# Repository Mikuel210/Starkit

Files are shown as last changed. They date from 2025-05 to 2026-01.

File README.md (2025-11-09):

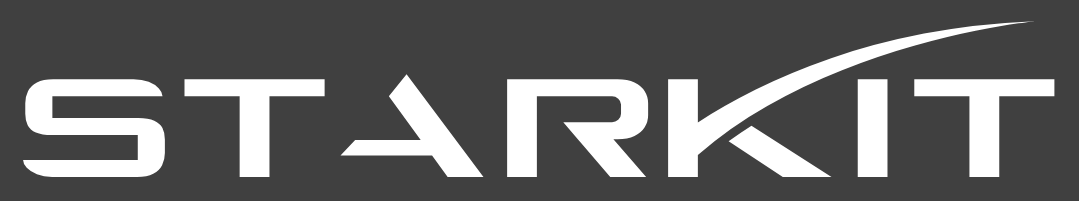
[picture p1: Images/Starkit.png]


Starkit is a thrust vector controlled electric model rocket designed for propulsive landings

<p align="center">
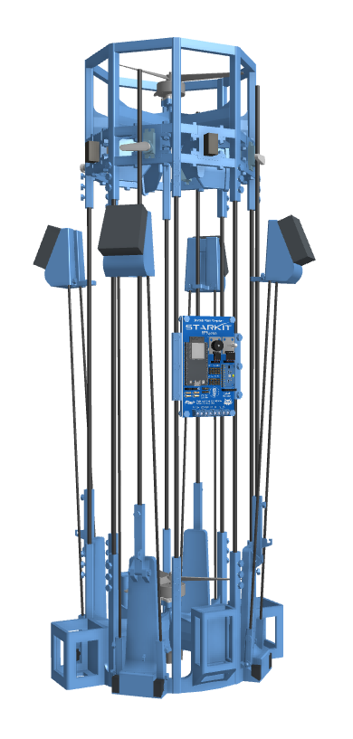
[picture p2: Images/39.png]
  
</p>

## Project description

I'm building an electric model rocket capable of taking off vertically, hovering and landing propulsively by using thrust vector control (TVC).

- **Propulsion**: I'm using two counter rotating brushless motors and 7" propellers. Each motor is powered by its own 6S LiPo battery and 60A ESC.
- **Avionics**: The main flight computer is an ESP32. I'm using an MPU9250 for orientation and a TF-Luna LiDAR for measuring altitude.
- **Control**: I'm using four TVC vanes driven by four Corona DS918MG servos.
- **Software**: I'm using PID algorithms for controlling orientation and altitude.
- **Structure**: The structure is built from 5mm carbon fiber rods. The rods are locked into 3D printed structural parts that hold mounts to attach the components as well.
- **Landing gear**: I'm using deployable landing gear, actuated by four SG90 servos. Each landing leg is made of a two part design that locks the leg in place once deployed.

## Goal of the project

**To learn and have fun by building an electric model rocket capable of lifting off, hovering and landing propulsively**

I want to build a fully reusable vehicle capable of landing propulsively through thrust vector control. If the rocket is capable of performing a 1 meter hop and hover for 30 seconds, I will consider it a success.

### Why I'm building this project

- To learn about avionics and PCB design
- To learn about software, communication and control systems
- To learn about rocket design
- To learn about CAD and project planning

## PCB

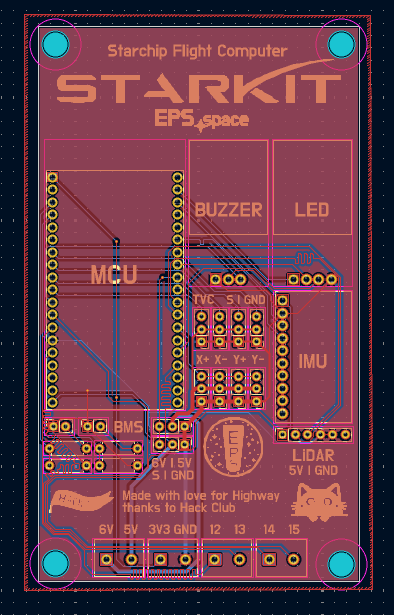
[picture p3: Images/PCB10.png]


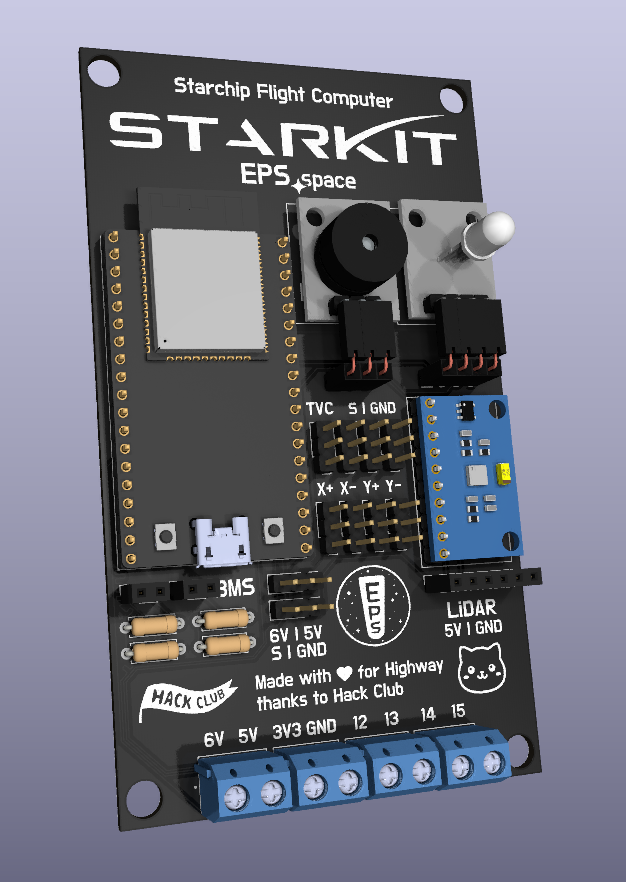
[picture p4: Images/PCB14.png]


## Wiring diagram

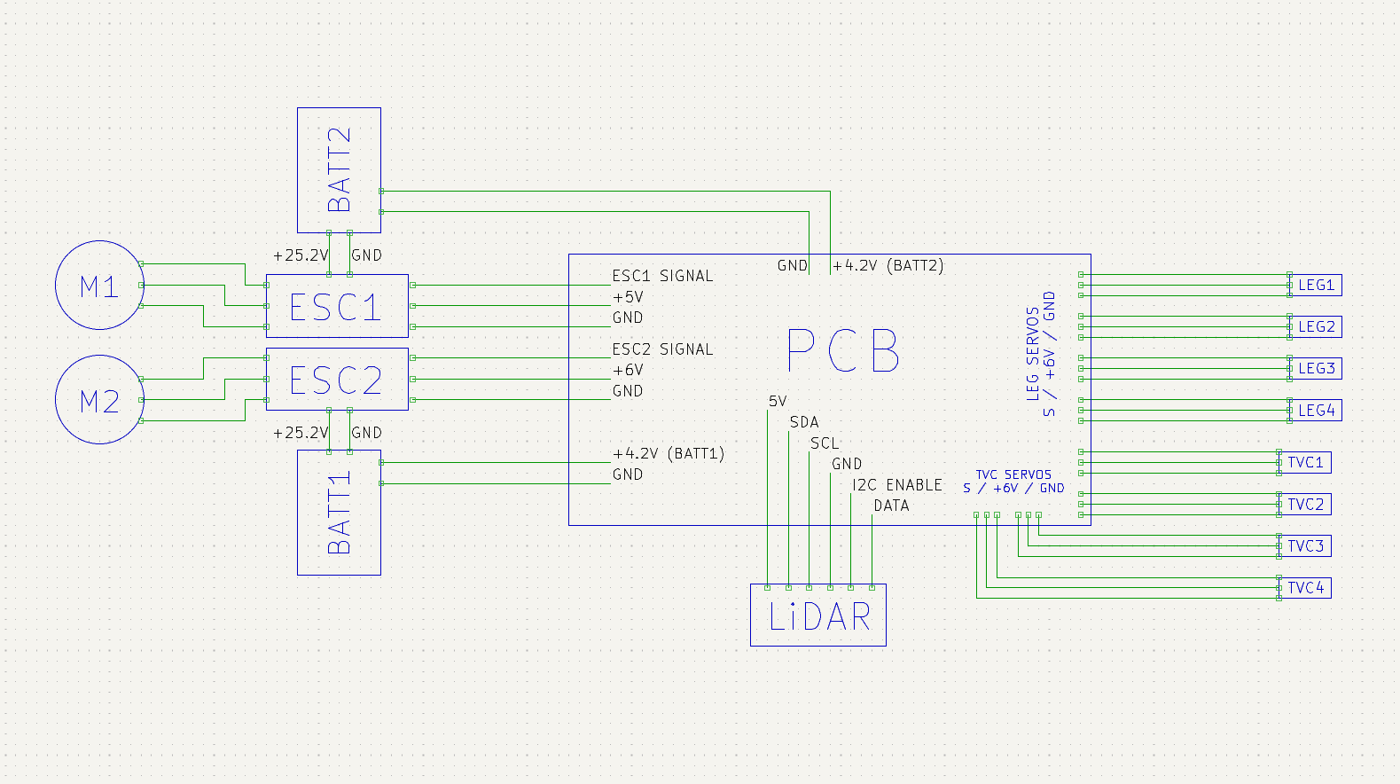
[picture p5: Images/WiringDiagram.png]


## BOM

| Item | Amount | Amount owned | Amount needed | Unit price (€) | Total price (€) | Link | Configuration |
| --- | --- | --- | --- | --- | --- | --- | --- |
| Batteries | 2 | | 2 | 21,50 € | 42,99 € | https://www.amazon.es/HRB-reemplazo-bater%C3%ADa-helic%C3%B3pteros-multicopter/dp/B08TBQKL5B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 | |
| ESCs | 2 | | 2 | 18,59 € | 37,18 € | https://es.aliexpress.com/item/1005007477046035.html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 | Flier 60A V2 |
| Motors | 2 | | 2 | 19,59 € | 39,18 € | https://es.aliexpress.com/item/1005005975992937.html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 | 1PCS KV1300 |
| Propellers | 2 | | 2 | 2,50 € | 5,00 € | https://immersion974.com/products/2-paires-dalprop-racerstar-cyclone-t7056c-7056-7x5-6x3-longue-portee-fpv-courses-helice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 | |
| Leg servos | 4 | 2 | 2 | 1,07 € | 2,13 € | https://es.aliexpress.com/item/1005006572297006.html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 | 2Pcs 180 Degree |
| TVC servos | 4 | | 4 | 9,64 € | 38,55 € | https://es.aliexpress.com/item/1005002272302617.html | With 25mm arm x4 |
| Structure rods | 20 | | 20 | 2,03 € | 40,50 € | https://es.aliexpress.com/item/1005004263451845.html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 | 5Pcs 5.0x500mm |
| Leg struts | 8 | | 8 | 0,77 € | 6,19 € | https://es.aliexpress.com/item/1005004263451845.html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 | 10Pcs 3.0x500mm |
| Leg springs | 4 | | 4 | 0,43 € | 1,73 € | https://es.aliexpress.com/item/4000250320601.html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 | 30mm 0.3 x 4 |
| PETG filament | 1 | 1 | 0 | 16,99 € | 0,00 € | https://eu.store.bambulab.com/es/products/petg-translucent?id=49192018149724 | |
| Velcro | 10 | | 10 | 0,15 € | 1,53 € | https://es.aliexpress.com/item/1005008063390791.html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 | Rectangle 16x70mm 10pcs |
| Bullet connectors | 6 | | 6 | 0,28 € | 1,66 € | https://es.aliexpress.com/item/1005006400659486.html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 | 6Pair 4.0mm |
| Cable for motor extension | 1 | | 1 | 5,59 € | 5,59 € | https://es.aliexpress.com/item/1005006566120439.html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 | 3m 12 AWG |
| Heat shrunk tubing | 1 | | 1 | 4,46 € | 4,46 € | https://es.aliexpress.com/item/1005005188307524.html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€%210%2C99€%21%21%21%21%21%40211b612817500001384372689ec846%2112000032032038883%21btf%21%21%21&afTraceInfo=1005005188307524__pc__c_ppc_item_bridge_pc_main__IQwes0f__1750000138532&gatewayAdapt=glo2esp | 580pcs in box |
| Cable for components | 1 | | 1 | 2,44 € | 2,44 € | https://es.aliexpress.com/item/1005006566120439.html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 | Black 5M 20AWG |
| Charger | 1 | | 1 | 19,67 € | 19,67 € | https://es.aliexpress.com/item/1005007326920235.html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 | |
| LiPo bag | 2 | | 2 | 5,56 € | 11,12 € | https://www.amazon.es/KUBDPQOR-bater%C3%ADa-Ign%C3%ADfuga-Explosiones-Proteger/dp/B0D6WDVMMQ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 | |
| PCB | 1 | | 1 | 0,00 € | 0,00 € | https://jlcpcb.com/es/ | |
| LiDAR | 1 | | 1 | 16,93 € | 16,93 € | https://es.aliexpress.com/item/1005007773724655.html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,scm-url:1007.40196.439370.0,pvid:257a845b-bd4b-41b9-8eb4-32116a834614,tpp_buckets:668%232846%238112%231997&pdp_ext_f=%7B%22order%22%3A%22236%22%2C%22eval%22%3A%221%22%2C%22sceneId%22%3A%2230050%22%7D&pdp_npi=4%40dis%21EUR%2157.01%2116.91%21%21%21460.14%21136.51%21%40211b680e17505431540684235eaa38%2112000042158078686%21rec%21ES%21%21ABX&utparam-url=scene%3ApcDetailTopMoreOtherSeller%7Cquery_from%3A#nav-specification | |
| IMU | 1 | | 1 | 12,29 € | 12,29 € | https://www.amazon.es/MPU%E2%80%919250-giroscopio-magn%C3%A9tico-aceleraci%C3%B3n-medici%C3%B3n/dp/B0BJ31W6KR | |
| ESP32 | 1 | | 1 | 4,99 € | 4,99 € | https://es.aliexpress.com/item/1005008256121637.html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 | 32D-Type-C-1PCS |
| Buzzer | 1 | 1 | 0 | 0,75 € | 0,00 € | https://es.aliexpress.com/item/1005007592230799.html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 | |
| LED | 1 | 1 | 0 | 0,70 € | 0,00 € | https://es.aliexpress.com/item/1005006942561228.html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 | |
| Resistors | 4 | 4 | 0 | 0,19 € | 0,00 € | https://es.aliexpress.com/item/1005007345052730.html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 | |
| Headers | 1 | | 1 | 2,02 € | 2,02 € | https://es.aliexpress.com/item/4000873858801.html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 | |
| Angled headers | 1 | | 1 | 1,24 € | 1,24 € | https://es.aliexpress.com/item/1005008210852764.html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,scm-url:1007.40196.439370.0,pvid:2362691a-9cfa-40b6-b383-5963bc6e059a,tpp_buckets:668%232846%238110%231995&pdp_ext_f=%7B%22order%22%3A%22162%22%2C%22eval%22%3A%221%22%2C%22sceneId%22%3A%2230050%22%7D&pdp_npi=4%40dis%21EUR%211.24%210.99%21%21%211.39%211.11%21%4021038df617505419994764643e6b41%2112000044248658299%21rec%21ES%21%21ABX&utparam-url=scene%3ApcDetailTopMoreOtherSeller%7Cquery_from%3A | 5Pin 5PCS |
| Screw terminals | 4 | | 4 | 0,37 € | 1,48 € | https://es.aliexpress.com/item/1005003556955422.html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 | 2Pin 5Pcs |
| Magnetic balancer | 1 | | 1 | 10,52 € | 10,52 € | https://www.amazon.es/Hobbypower-Multirotor-Propeller-Magn%C3%A9tico-Quadcopter/dp/B00GSKSFM6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 | |
| TOTAL | | | | | 309,39 € ($359.67) | | |

***

Made with ❤️ for Highway thanks to Hack Club

A badge of a Cerberus and a raccoon laughing together, with the text "HIGHWAY" and "HACK CLUB" beside them.

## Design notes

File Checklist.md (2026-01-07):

- [x] Choose a propulsion system
- [x] Choose a TVC method
- [x] Choose a structure and landing legs
- [x] CAD and simulate a 7" build
- [x] Choose avionics components
- [x] Choose servos
- [x] Choose motors, propellers and ESCs
- [x] Choose batteries and charger
- [x] Create BOM
- [x] Design PCB
- [x] Revision
- [x] Optimize PCB to use a single ESC pin and maybe use a 38 pin ESP
- [x] How am I going to cut the rods
	- Tape, hacksaw, 3D printed clamp, respirator
- [x] How am I going to build the test stand
	- Wood, bearings and 3D prints
- [x] Stuff in the diary
	- [x] Rod locking to prints
- [x] RC groups feedback
- [x] README

## After submitting

- [-] Check diameter of launch mount rails
- [x] Prototype attachments and servo mounts
	- [x] Update servo mounts to use a glued part that bolts into the thing

## After getting the grant

- [x] Buy everything except PCB
- [x] Test avionics
	- [x] Test LiDAR
	- [x] Test IMU
		- [x] Solder!
	- [x] Test TVC servos
	- [-] Make PCB circuit
- [x] Measure parts and order PCB (w/ conformal coating)
- [x] Solder PCB
	- [x] Make sure to angle the IMU headers at an angle
- [x] Prototype legs
	- [x] Change design to use bend & 500mm rods
	- [x] Update tolerances and spring thingies
	- [x] Make test pieces
	- [x] Prototype
	- [x] Change design for 500mm rods
	- [x] Reprint parts, adjusting tolerance
	- [x] Print assembly, adjust vertical tolerances
	- [x] Print deployment assembly
	- [x] Update bolt tolerance
	- [x] Make servo arm longer
	- [x] Consider foam to reduce vibrations
	- [x] Paste rods to prints tentatively
	- [x] Testing
- [x] Test PCB
- [x] Solve rod locking to prints. Test glue and bolt lock.
	- [-] Test acetone for removing resin from rods
- [x] Prototype battery, motor, rod, LiDAR, vane and ESC mounts
	- [x] Battery mount
	- [x] ESC mount
	- [x] Is the cable long enough?
	- [x] LiDAR mount
	- [x] Rod bolt attachment test
	- [x] Motor mount test
	- [x] TVC vanes (already tested for servo arm extension)
	- Conclusions
		- [x] Evaluate how much taller I can make the battery mount without interfering with the cables
		- [x] Evaluate velcro behavior
		- [x] Evaluate does the prop fit??
		- [x] I have to buy XT60 extenders because the cable isn't long enough and I don't have enough margin to move the mounts. A 3cm extension is fine (though I would check again before buying)
		- Bolt locking rods is the new standard
		- Required adjustments
			- [x] 0.5 tolerance for rods
			- [x] 5mm taller than prototype for the battery mount
			- [x] Bolt locking for all rods
			- [x] 0.5mm less width battery mount
			- [x] 1mm more width ESC mount
- [x] New CAD model
	- [x] Increased diameter
	- [x] Bolt lock is the new standard
	- [x] New airflow straighteners
	- [x] Only 1 rod segment
	- [x] Foam on the landing legs to reduce vibrations
	- [x] LiDAR under motor? 
- [-] Print another middle assembly section to test rod attachments and bolt tolerances
- [x] Decide if layout has to be changed
- [x] Test motor attachment
- [/] Printing and assembly
	- [/] Printing
		- [x] Buy filament
			- [x] Check in on Clutter grant
		- [/] Propulsion module
			- [x] Rod bolts
				- [?] Reprint them with less tolerance
			- [/] Landing legs
				- [x] Consider switching to 5mm rods
				- [-] Reprint leg tops in order to get a lower locking angle
				- [x] Reprint leg bottoms and potentially leg tips to get a stronger grip on the rods
				- [x] Redesign leg tips and bottoms for a stronger grip and straighter bolts
				- [x] Redesign leg bottom bolt
				- [x] Reprint leg parts
				- [/] Iterate on shock absorbers
				- [/] Print updated leg tip, bolts with more tolerance and cylinder with less tolerance
				- [ ] Hot glue together the perfect leg
		- [x] Guidance Assembly
			- [x] Rod bolts
			- [x] PCB bolts
		- [ ] Control assembly
			- [ ] Buy PETG
			- [ ] Rod bolts
			- [ ] Servo attachments
	- [ ] Assembly!
	- [ ] Cables
- [ ] Test motors
- [ ] Balance propellers
- [ ] Test motors w/ propellers (@ 90% thrust, they can overheat)
- [ ] Test stand assembly and PID tuning
	- [ ] Idea: Let the thing fly but tethered
- [/] Flight software
	- [x] TVC PID
	- [x] Altitude PID
	- [x] Fix TVC wiggle
	- [x] State machine
	- [x] Continuous angle (breaks at 180)
	- [x] Actuate TVC
	- [ ] Unity Simulation
		- [ ] Communication
	- [ ] Fuse altitude
	- [ ] Add BMS
		- [ ] Calibrate ADC
- [ ] Simulation
- [ ] Countdown software
- [ ] FLY IT
	- [ ] micros() will overflow after 1 hour

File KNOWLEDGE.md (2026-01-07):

**When encountering an obstacle, pause to analyze root causes instead of immediately trying random fixes.**
**Work on focused, uninterrupted sessions with no multitasking.**
**Do not cut on drying time**
**Always make test pieces before printing full parts**
**Test pieces don't always behave like full parts. Oversize holes and use another locking mechanism.**
**Don't go below the width of auto brims.**
**Do not force fits.**

Printing orientation affects the fit massively
A longer hole means more friction

- Carbon rod tolerance -> 0.5 total, use bolt
- Bolt tolerance: 0.2 -> 0.4 total

Max. spring length: >= 14cm

PLA requires ears

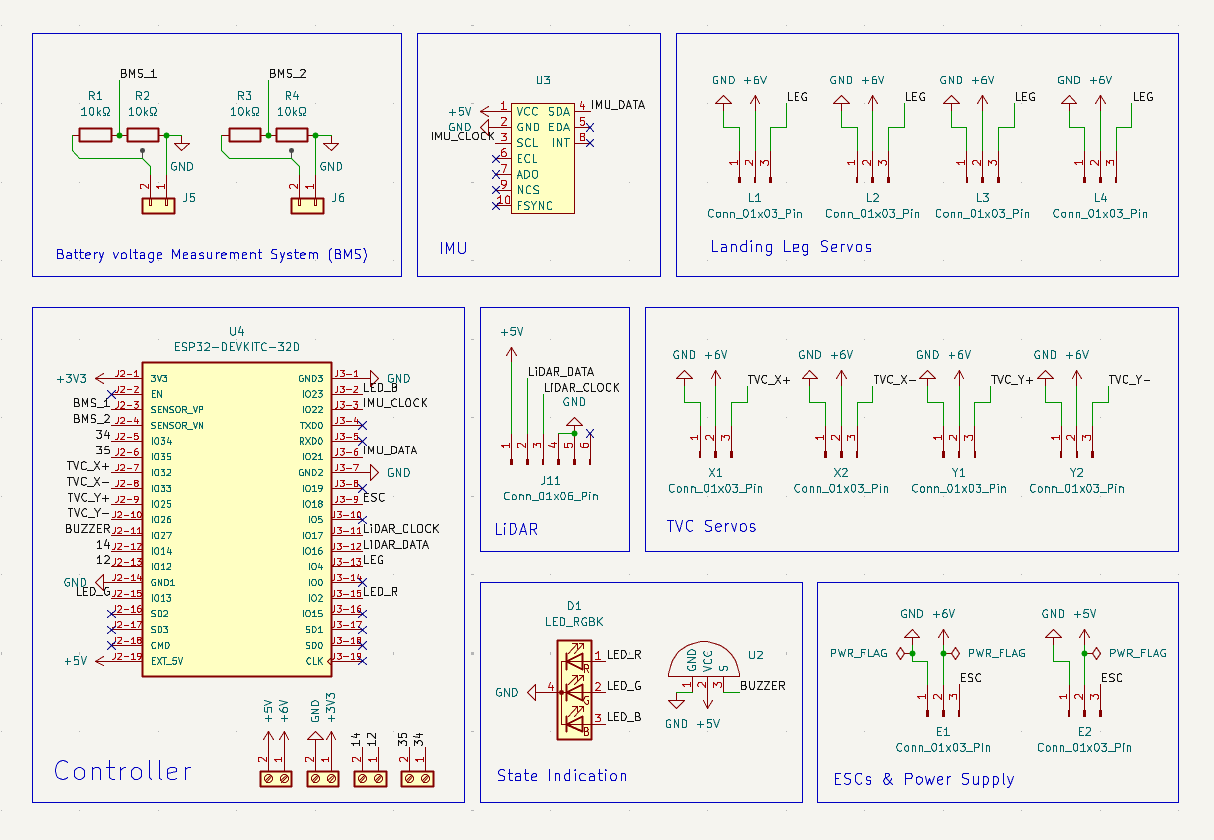
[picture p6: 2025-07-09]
Images/Schematic.png

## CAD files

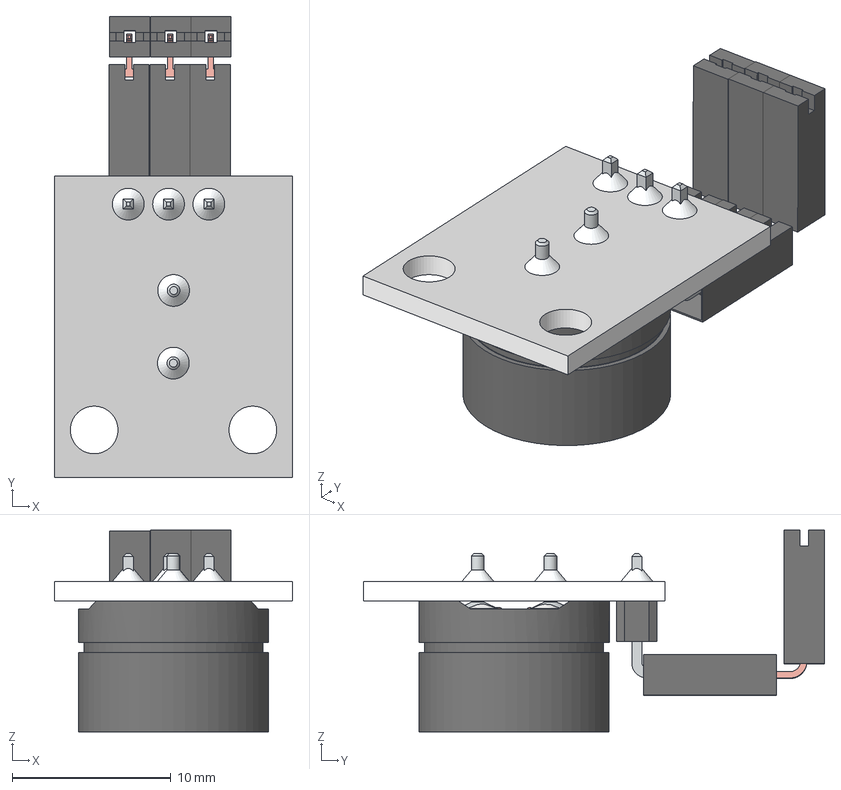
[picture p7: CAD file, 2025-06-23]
PCB/Dependencies/Buzzer.step
15.0 x 29.1 x 12.7 mm

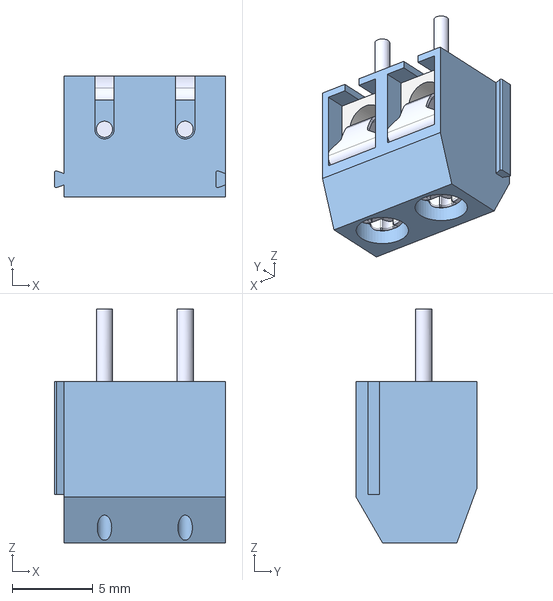
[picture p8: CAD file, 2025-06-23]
PCB/Dependencies/KF301-2P/KF301-2P.step
10.6 x 7.50 x 14.5 mm

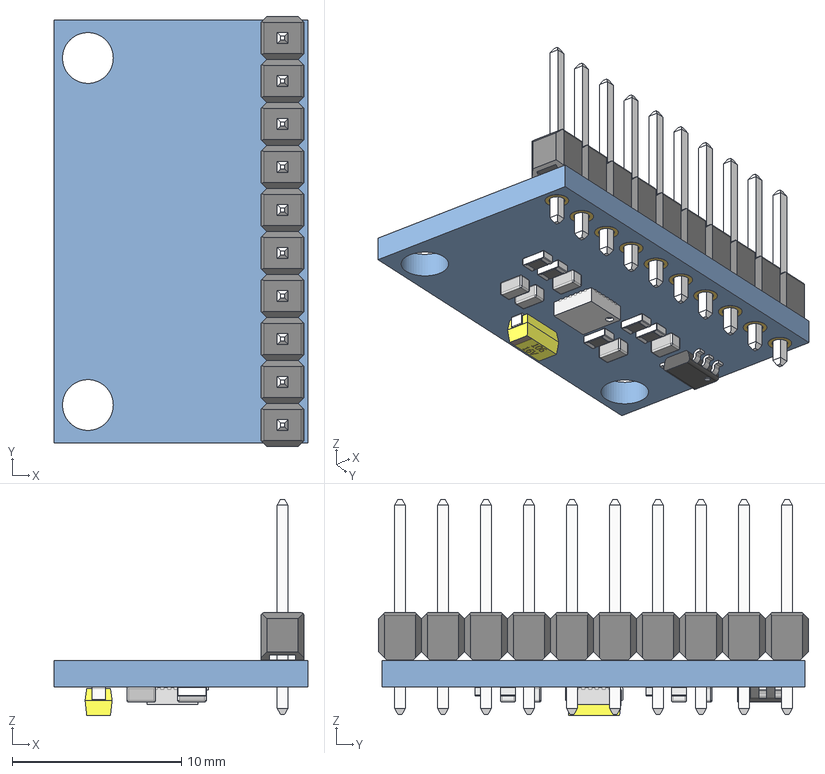
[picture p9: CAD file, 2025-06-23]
PCB/Dependencies/MPU-9250.step
15.0 x 25.4 x 12.8 mm
Pin Header 1x10 TH Pitch 2.54mm x 20
RESC-0603 x 15
CAPC-0603-T0.9-BN x 5
hole_plating x 20
tantalum 10uF
board
SOT23_5
QFN-24 3x3 0.4mm

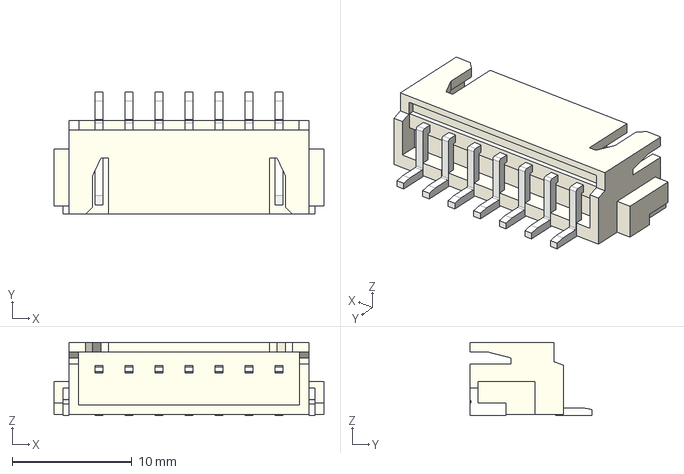
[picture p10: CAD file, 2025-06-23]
PCB/Dependencies/JST-XH7-SMD.step
22.5 x 10.2 x 6.10 mm

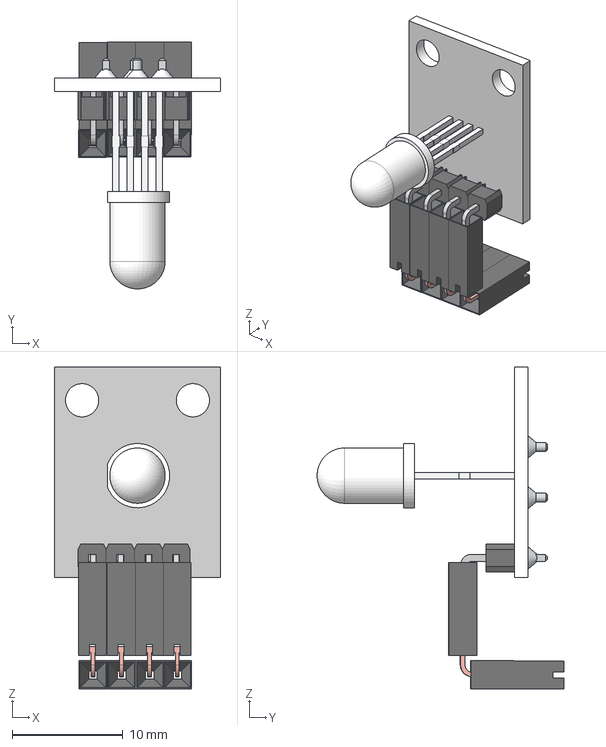
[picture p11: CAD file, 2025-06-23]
PCB/Dependencies/KY-016.step
15.0 x 22.3 x 29.1 mm

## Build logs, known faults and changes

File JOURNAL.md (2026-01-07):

---
title: "Starkit"
author: "Miguel"
description: "A thrust vector controlled electric model rocket designed for propulsive landings"
created_at: "2025-05-20"
---

## May 22: Initial ideas and goal of the project

I always like to begin engineering projects by setting a goal. For this project, my goal is the following:

**To learn and have fun by building an electric model rocket capable of lifting off, hovering and landing propulsively**

I want to build a fully reusable vehicle capable of landing propulsively through thrust vector control. If the rocket is capable of performing a 1 meter hop and hover for 30 seconds, I will consider it a success.

Based on my vision for this project, I've set some design requirements. This way, I will try to find the most efficient and cost-effective way possible of creating something that I'll be happy with:

### Design requirements

These are the absolute musts that a design should have:

- The rocket is powered by electric propulsion for cheap and safe flights and fast turnarounds
- The rocket is fully reusable and uses thrust vectoring to lift off, hover and land propulsively
- The rocket can perform a 1 meter hop and hover for 30 seconds
- The rocket is modular

  - Components are easily accessible and replaceable
  - The rocket is designed for a future launchpad integration

    _If I achieve reliable landings, I might try to build a launchpad to launch and catch the rocket from. The rocket should be modular and be designed with this in mind._

    - The rocket has got detachable or deployable landing legs and attachable catch pins
    - The pad should be able to hold the rocket until full throttle is reached

### Dream goals

These are not essential but they'd be cool to have:

- The rocket can perform a 10 meter hop
- The rocket can hover for a minute
- The rocket looks as cool as possible

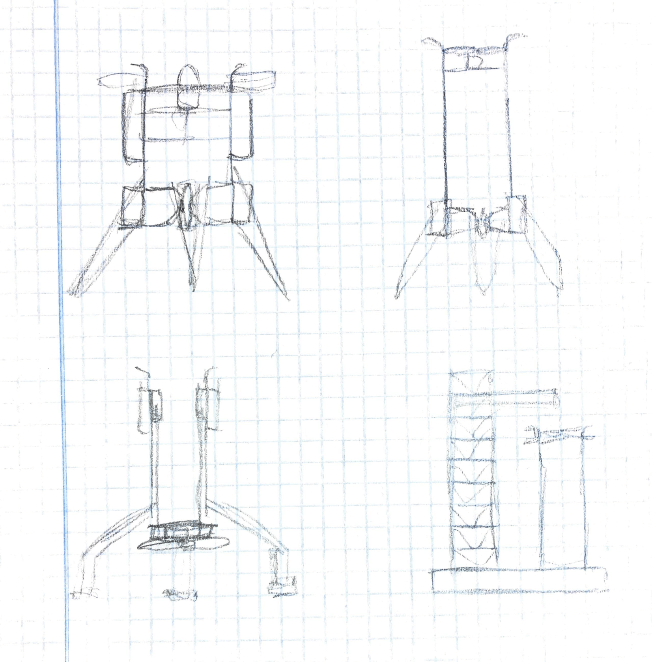
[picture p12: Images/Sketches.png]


_Initial ideas and concepts of possible designs_

**Time spent: 1h 15min**

## May 24 Log 1: Research on propulsion systems

I've decided to choose a propulsion system first and then work around that. Some options I think would fit this project are:

- Single EDF (Electric Ducted Fan)
- Single propeller
- Counter-rotating propellers
- Ducting a propeller(s) myself

The main things I've learnt today are:

- Ducting a propeller can increase efficiency and thrust.
- EDFs take advantage of this. An added benefit is that they often have stator vanes that minimize the torque produced by spinning the propeller.
- A larger propeller is usually more efficient and provides more thrust. A larger propeller could match the thrust of a smaller EDF while being less expensive, however the torque and gyroscopic effects become greater the more you scale the propeller.
- If I use a single propeller I probably wouldn't want to duct it myself as it could actually decrease the performance (EDFs are propeller and duct combinations specifically made to work together).

I've discarded ducting a propeller myself. However, I still have to make more research to figure out what the best option is. If I manage to overcome the gyroscopic effects, a single propeller would be a nice option over an EDF, as it would be less expensive. Counter-rotating propellers would also be a good option as they cancel their torque, but I still have to research if the thrust of two propellers in series is just the sum of their individual thrust.

**Time spent: 2h 30min**

## May 24 Log 2: Research on counter-rotating propellers

The reasons I would choose counter-rotating propellers over a single propeller are:

1. They cancel their torque, which means that they don't apply any rotational force to the vehicle and you don't have to worry about gyroscopic effects.
2. You have some control authority in the roll axis. If the rocket gains angular speed, you can correct it by adjusting the throttle of each individual motor. This also allows me to only use 2 servos for TVC, as you only need to correct 2 axis.

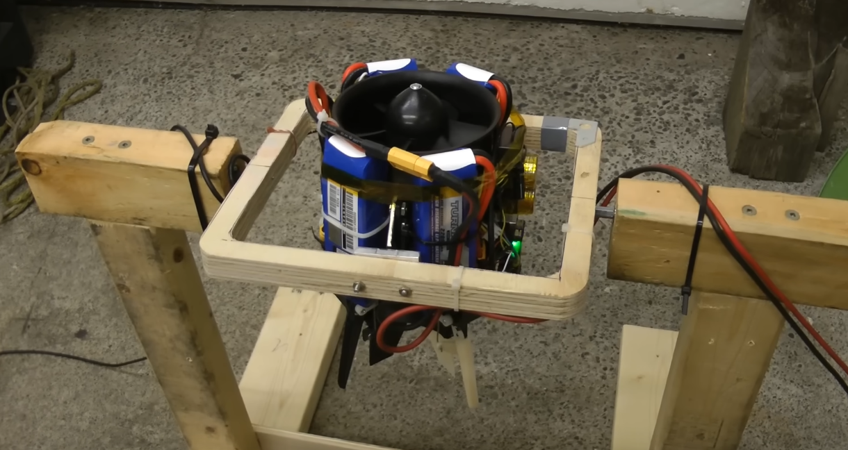
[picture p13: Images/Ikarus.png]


_The Ikarus model rocket had an issue where whenever it wanted to apply a torque through TVC, it had to apply a perpendicular torque as well due to the gyroscopic effects of a single propeller. In the Ikarus II rocket this problem was solved by using counter-rotating EDFs._

Placing the propellers one after the other would decrease thrust and efficiency. However, if I keep the propellers spaced and use airflow straighteners for feeding the second propeller cleaner air, this could be mitigated.

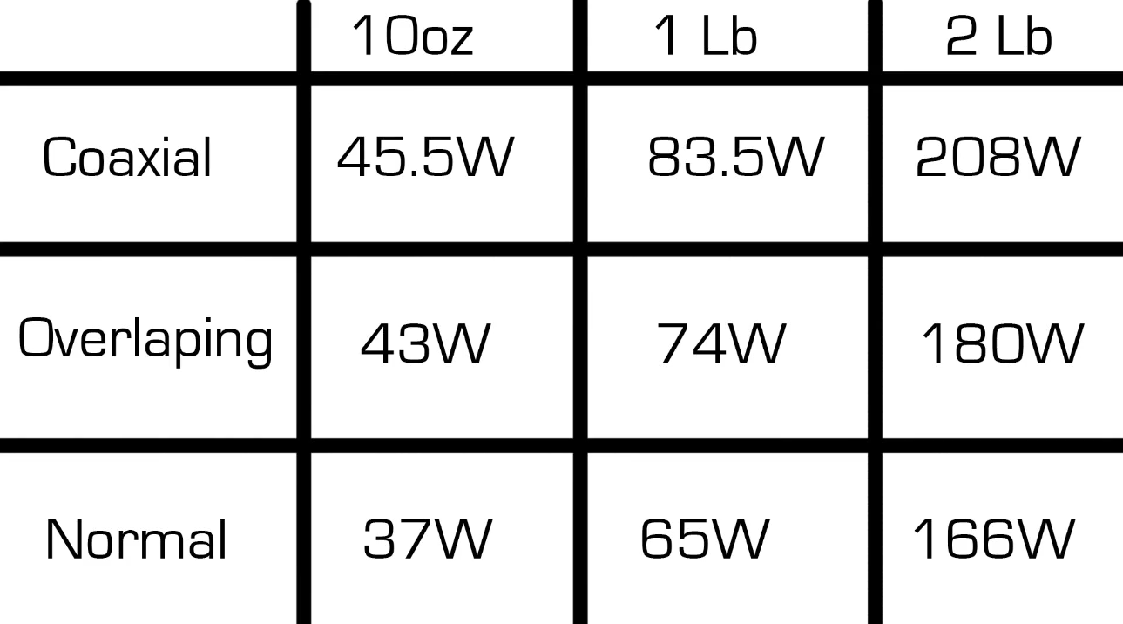
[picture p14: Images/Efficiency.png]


_Test on the efficiency of normal, overlapping and coaxial propellers. Coaxial propellers are about 80% of the efficiency at a low spacing. Source: https://www.youtube.com/watch?v=tFJyE3Uns3o_

If I want to get as much thrust as possible in this configuration, I should use a higher pitch in the rear propeller. However, I don't think this is a good idea as there aren't many high pitch propeller options or test data, and using different propellers might cause them to rotate at different speeds, which could cause a torque in the vehicle.

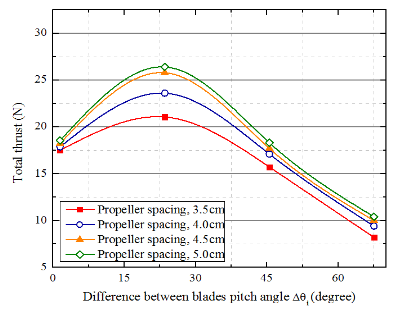
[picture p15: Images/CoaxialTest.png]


_Test showing the thrust of different propeller spacings and rear propeller pitch difference. Source: https://www.icas.org/icas_archive/ICAS2014/data/papers/2014_0072_paper.pdf According to https://drones.stackexchange.com/questions/1209/do-propellers-layered-on-top-of-each-other-have-twice-the-thrust-of-one-propelle, you can get almost the full thrust if you increase the pitch of the rear propeller._

I'll have to do more research to figure this out, nonetheless I think counter-rotating propellers are a really good option.

**Time spent: 1h 30min**

## May 25: Deciding on counter-rotating propellers

After some research I’ve decided that using two identical counter-rotating motors and propellers is the best option. You avoid torque and gyroscopic effects that you would have with a single propeller or EDF, and you still can get their full efficiency by placing them side by side. However, I'll have to see if even with the structural weight that would add placing the propellers side by side, this configuration would outperform placing the propellers one after the other.

https://www.youtube.com/watch?v=VsyFejn40Ss

This video shows a vehicle with a similar configuration to what I was thinking. However, TVC roll control is later added because adjusting the throttle of each motor is not enough and causes the rocket to lose thrust.

I could test the thrust of the motors at different throttle levels to try and avoid this, but either way I think adding TVC roll control would be better. In the future the rocket could need precise roll control if I attempt to build a catch tower.

**Time spent: 1h**

## May 27 Log 1: Deciding a motor configuration

I've made a spreadsheet for calculating the thrust to weight ratio (TWR) of a coaxial and a side by side configuration.

For the coaxial configuration, I'm picturing a cylindrical structure with a propeller at the top and another at the bottom. For the side by side configuration, I'm thinking of 2 of such structures next to each other, with one propeller each. Note that this isn't necessarily the only way of placing the propellers one next to the other, but I want to keep a shape that can integrate nicely with a launch mount and a catch tower.

For the calculations I've used a carbon fiber rod structure, 4 TVC vanes and 2 Emax ECO II 2807 motors with 7" propellers. I will have to research more in depth if these options are the best for the project, but so far the coaxial configuration has a better TWR.

There are many variables that I won't know until I pick all the parts and design the 3D models. The calculations will get more accurate as I do so, but for now I will be designing the rocket for a coaxial configuration.
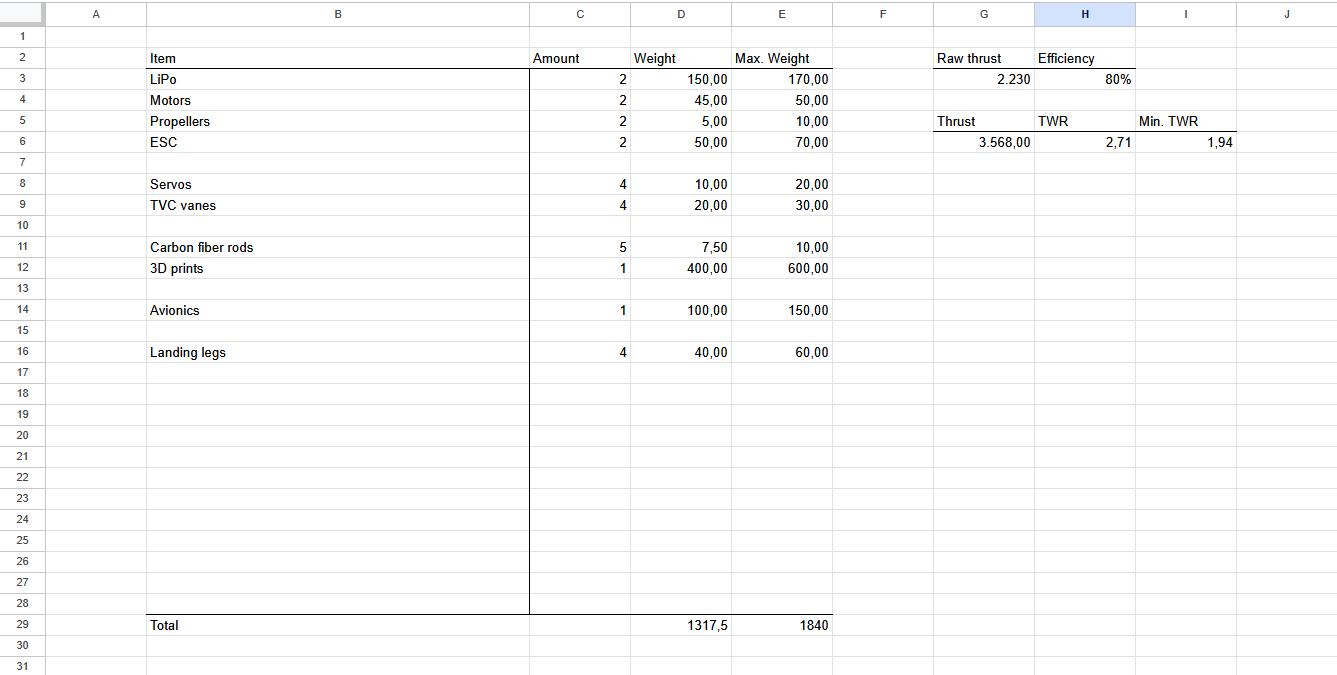
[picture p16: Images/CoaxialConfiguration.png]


**Time spent: 1h**

## May 27 Log 2: Choosing a TVC method

I had figured out previously that I need TVC roll control and I can't just rely on throttling the motors at different speeds. Because of this the only viable options I have are using 3 or 4 TVC vanes.

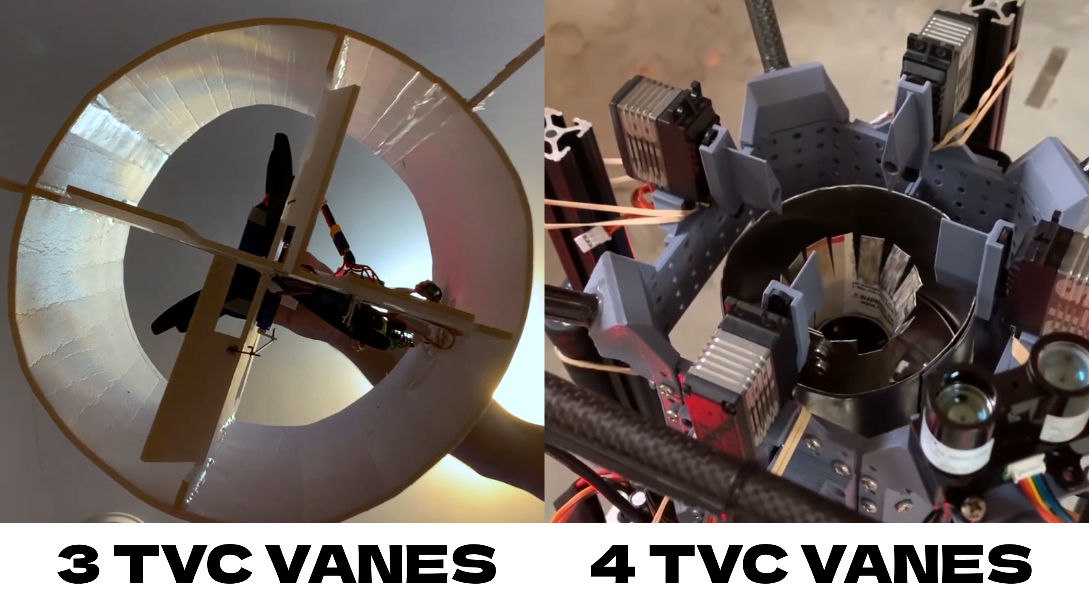
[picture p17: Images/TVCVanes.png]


Using 3 vanes would probably be slightly cheaper. Although it would probably be fine with 3, I've decided to go with 4. The reasons are:

- 4 vanes allow me to keep all axis identical, which simplifies tuning
- 4 vanes double the control authority in the roll axis, which improves stability
- A 3 vane system needs for one vane to be longer. A longer vane would probably need hinges or supports, adding complexity.
- There are very few examples of 3 vane systems, and I haven't found any for the thrust that I'm aiming for. This makes it harder to choose servos with the right amount of torque.
- I want to keep control over the length of the vanes for balancing control authority and airflow obstruction. This is harder with a 3 vane system, as one vane has to go all across.

I don't think using 4 vanes would mean any significant cost increase, but they are simpler, they provide more control and I have more design references, so I’ve chosen to go with that.

**Time spent: 1h 30min**

## May 28: Structure and general layout

For TVC to work properly you need the thrust vector to be far away from the center of gravity (COG). You want to place all the weight at the top and TVC the bottom motor or the other way around.

A lower COG is better for stability in landings. This means I would want to place all the weight at the bottom and use TVC in the upper motor. For this, I would need a structure without walls for the air to get out. Plus, as I had figured out earlier, I probably don't want the structure to act as a duct as it can decrease performance.

My first thought was using carbon fiber rods, which I've seen being used in similar projects. After researching some other options like balsa wood, I've come to the conclusion that carbon fiber is indeed the best option. It has a much better strength to weight ratio than others, and even though it would likely need stiffeners because it can flex, what I care about is that they provide strength with the minimum amount of volume so that they don't obstruct the airflow much.

**Time spent: 1h 15min**

## May 29: Research on landing legs

In the future I might build a launchpad to launch and catch the rocket from, which means I would need landing legs that are either deployable or detachable so that they don't interfere with the launch mount.

I think deployable legs would be a better option. They would allow me to test the launch mount before trying to catch the rocket, and they could even allow me to abort a catch if any readings are off. Deployable legs are also much cooler and a nice challenge.

After looking at some other projects I've come up with a design that would be reliable and cheap and easy to implement.

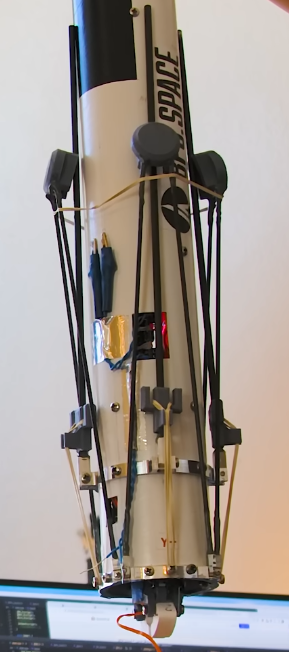
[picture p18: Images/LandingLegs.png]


_Landing legs of the Scout F rocket by BPS.space_

Similar to the image, landing legs in my rocket would have 2 carbon fiber struts with a 3D print at the top. A single strut would be pulled by a tension spring (a rubber band in the image) and would snap into the 3D print when deployed, locking the leg in place. Landing legs would be held in place with servos before deployment.

I will go with 4 landing legs. It's what I've seen being done the most and I think it's a nice spot between stability and weight.

**Time spent: 1h 15min**

## May 30: Starting the CAD design

Now that I know the general design and layout of the rocket, I've begun designing it in CAD. I don't know the parts that I'm going to use yet, but this model will help me refine my calculations. I'm designing for a 7" build, but if after making the CAD model and picking the parts I realize I have enough weight margin to scale down the motors or the whole vehicle, I will do that.

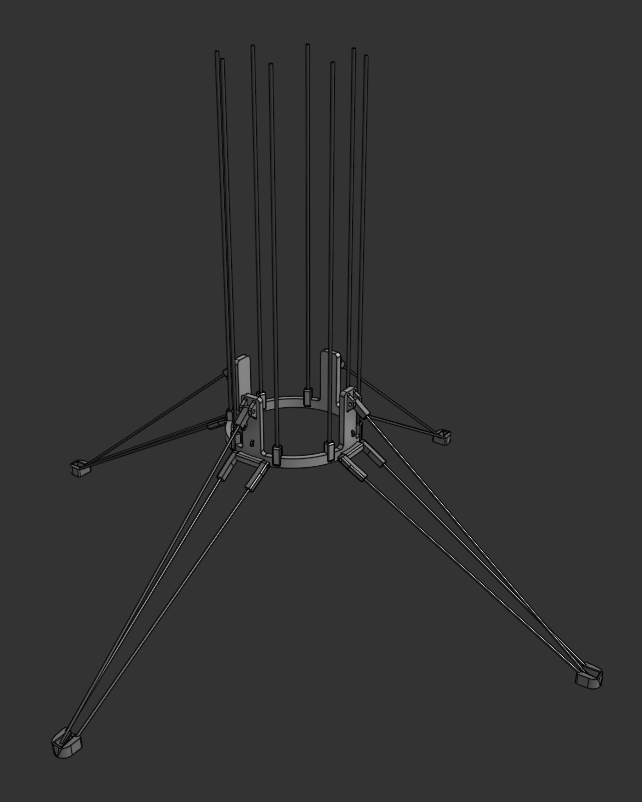
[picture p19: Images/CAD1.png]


I made a new Onshape document and began designing the base of the vehicle. I've almost finished making the landing legs. Tomorrow I plan on adding the bottom motor mount and rails for integration with the launch mount.

**Time spent: 4h 30min**

## May 31: Landing legs are finished

Today I've finished making the landing legs. I've added stoppers and bolts that will allow the parts to rotate into place.

I've also added the struts that will hold the bottom motor. These double as airflow straighteners, which probably isn't necessary. However I'm doing that on the top motor for feeding the bottom motor cleaner air, and I prefer to do it in both to ensure both motors behave the same and no torque is created.

Finally, I've begun making the part that will join the bottom and top rods of the main structure. This allows me to buy shorter rods which I've seen are the cheapest option, and this also makes the rods flex less. This part will hold the servos that hold the landing legs in place too.

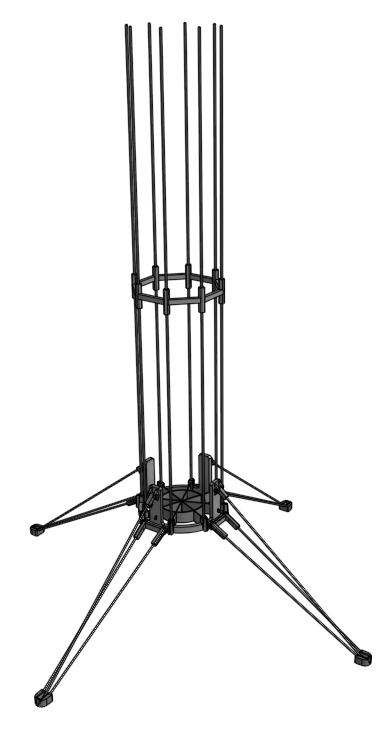
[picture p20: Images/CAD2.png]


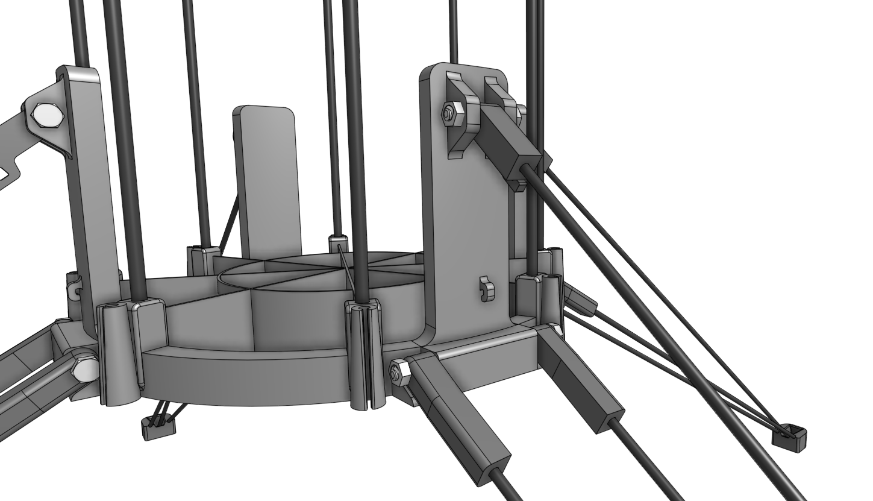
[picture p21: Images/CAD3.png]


**Time spent: 4h**

## June 1: Adding servo attachments

I didn't have a lot of time today but I've figured out how to attach the servos for deploying the legs to the 3D printed part. The servos snap into some slots and are then secured with two bolts.

Now, I only have to add holes to the landing pads for using a zip tie to attach the two parts of each landing leg. This way both can stay in place with a single servo. With this the leg deployment mechanism would be complete.

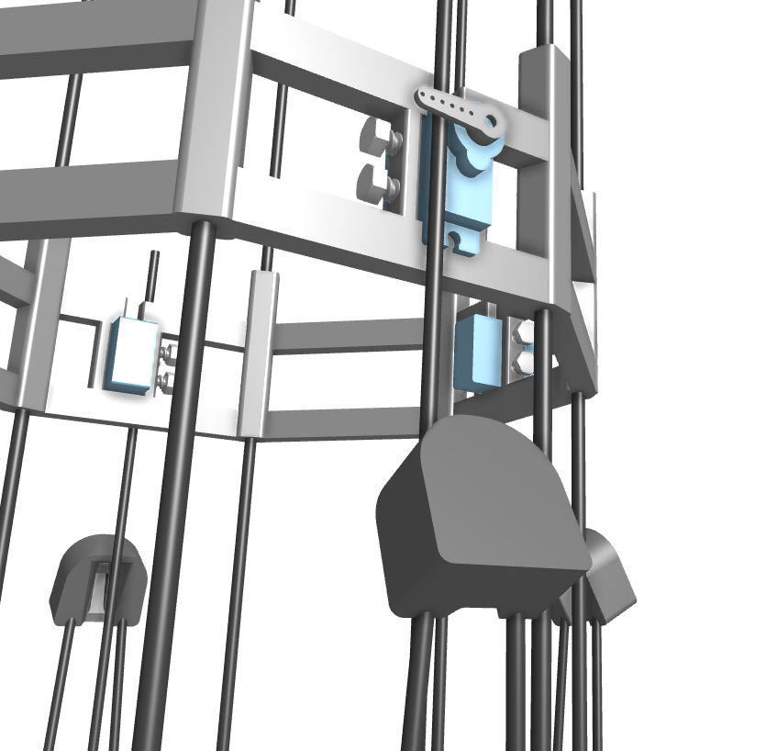
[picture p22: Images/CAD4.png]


**Time spent: 2h**

## June 2: Switching to thicker rods and completing the leg deployment mechanism

I should have probably checked how much carbon fiber rods flex at different diameters before starting the CAD model. It's really bad at 3mm. I've changed most rods to 5mm which should work a lot better.

I've also redesigned landing pads. This allows for them to be held closer to the structure before deployment, and it should also improve the reliability of the two parts of the legs locking together. I've also added a ring that attaches the two parts of landing legs, avoiding the need of using a zip tie.

With this I've finished making the leg deployment mechanism. Next, I'll make the part for holding the upper motor and TVC servos.

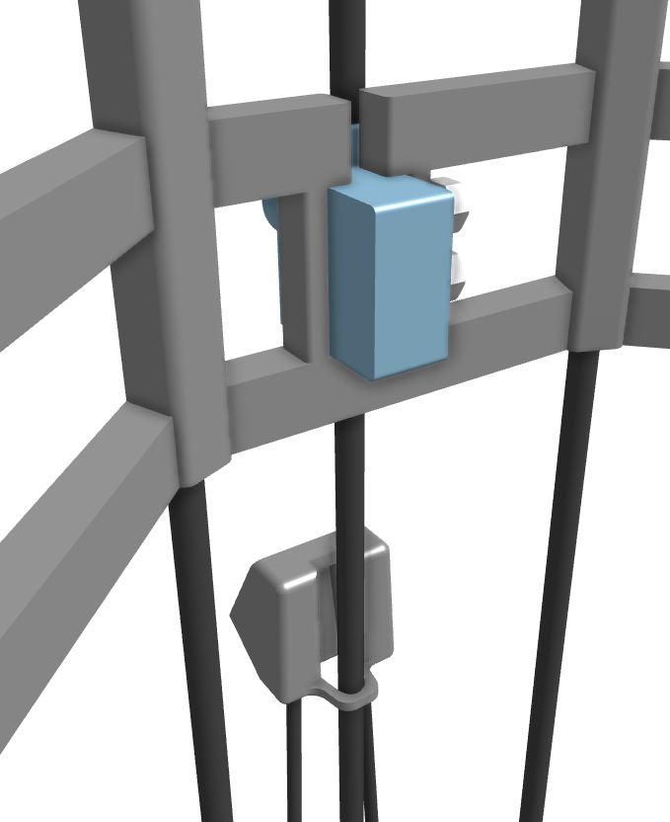
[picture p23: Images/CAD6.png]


**Time spent: 2h**

## June 4: The CAD model is taking shape

Today I've made the top assembly that holds the upper motor and the 4 servos with TVC vanes. I've chosen to use Corona DS-919-MG servos, as they are fast and precise; and Emax ECO II 2807 1300KV motors, as they provide the most thrust for their range at a really affordable price too.

Next I'll make mounts for the batteries, ESCs, PCB and motors (right now they're on top of the struts and they need a mount to be screwed on). With this I should be able to slice the models to know their weight and calculate the TWR of the rocket.

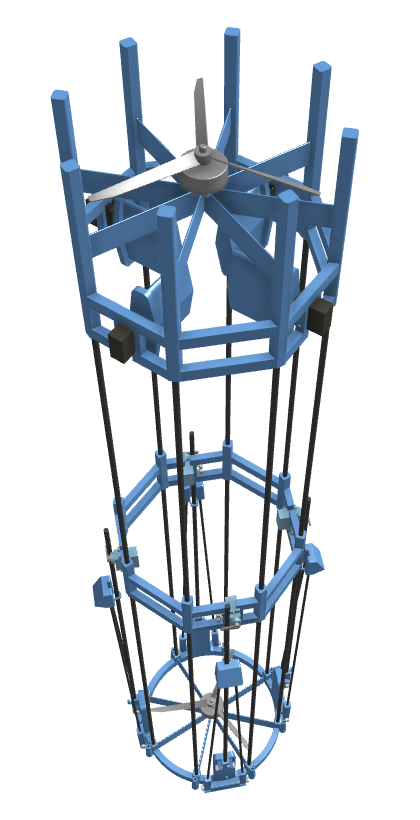
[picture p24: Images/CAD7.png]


**Time spent: 3h 30min**

## June 6 Log 1: The CAD model is finished!

Today I've made the battery, ESC, PCB and motor mounts. I've also added attachments for catch pins and for securing the rocket to a test stand which I plan on using for tuning the control system.

With this the CAD model is finished. I've sliced all of the parts and determined that the TWR of the rocket is around 2. This is in the range that I was hoping for, as I want to have margin for if the rocket ends up weighing more or it produces less thrust. I will keep it at this scale and with a coaxial configuration, as it's simpler and has a similar TWR.

Next, I will do more research on batteries and ESCs to see if what I've been using for now is the best option. After this I will begin designing the avionics and prototyping mounts and attachments.

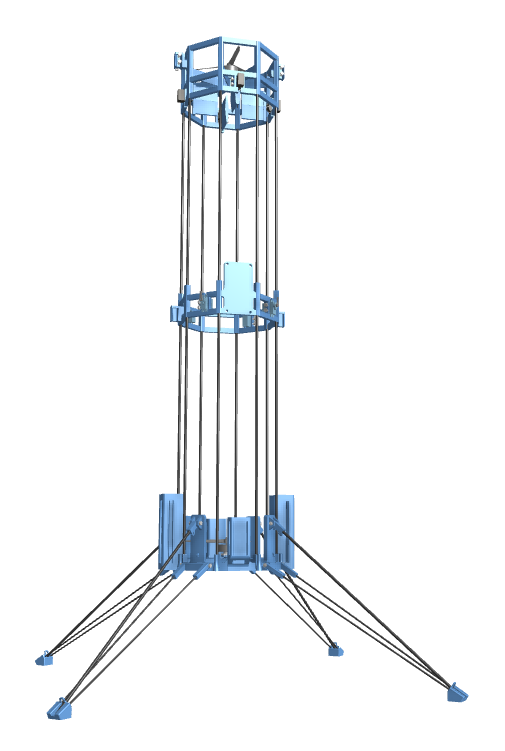
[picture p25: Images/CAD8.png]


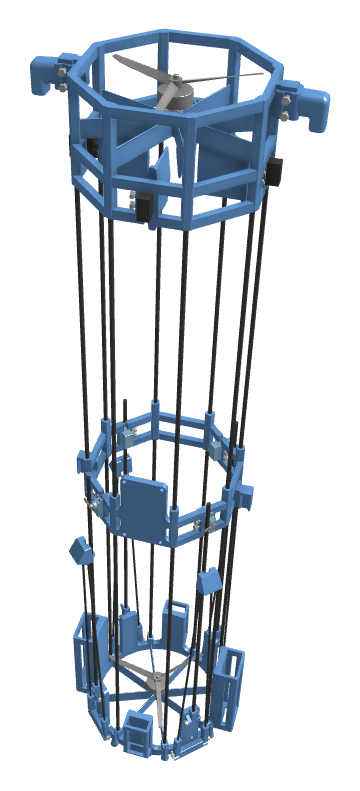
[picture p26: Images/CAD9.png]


**Time spent: 4h**

## June 6 Log 2: Research on batteries and ESCs

I've decided to switch from two 3S batteries to two 6S batteries. This simplifies wiring, as I would have to find a way to connect the 3S batteries in series while keeping the cables as short as possible, as making them longer could damage the ESCs.

For the ESCs I've chosen to use the SURPASS HOBBY Flier 60A, as it's cost effective and it provides a 6V 8A output to power the rest of components.

**Time spent: 1h 30min**

## June 7: Research on avionics + beginning making the BOM and PCB

Today, I've made research on avionics components and chosen to use the following:

- **Controller**: I've chosen the ESP32 as it gives me enough processing power and built in communications
- **Altitude measurement**: I've chosen the TF-Luna LiDAR, as it's accurate and doesn't drift over time. While this sensor limits hops to up to 8 meters instead of the 10 meters I was aiming for, I think this is a fair tradeoff as upgrading to a 10 meter LiDAR would be twice as expensive.
- **Orientation**: I've chosen to go with an MPU-9250 IMU (Inertial Measurement Unit), as it's cost effective and widely used
- **Communications and data logging**: I will use Bluetooth, provided by the ESP32. I will monitor data and control the launch countdown from a laptop and the data stream will be saved on the computer.
- I will also use a voltage regulator for the LiDAR, resistors for measuring the voltage of the batteries and an LED and a buzzer for state indication

With this, I've updated the CAD model to house the new components:

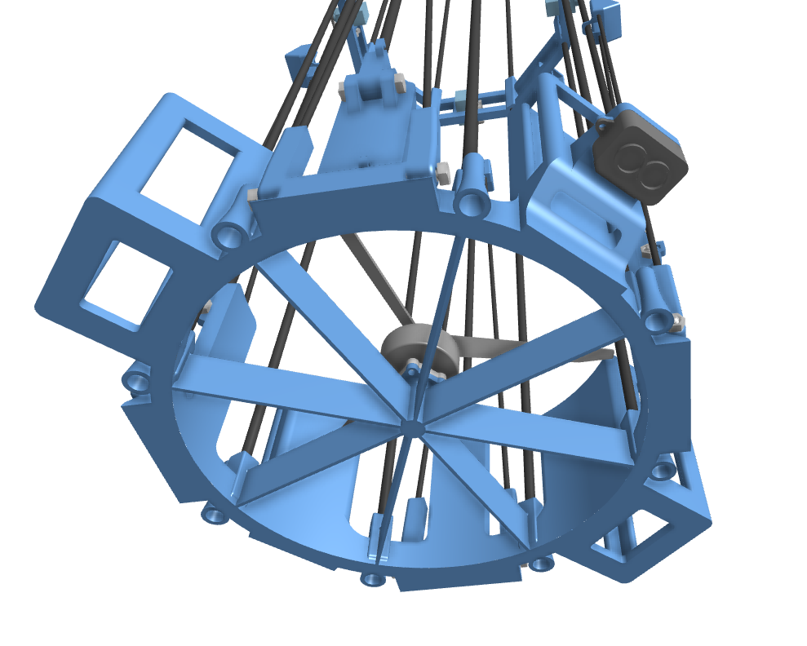
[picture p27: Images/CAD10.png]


Next, I've begun making a BOM so that I can keep track of the price and the weight of all components. I've also chosen a charger, a LiPo bag, a magnetic propeller balancer and extension cables and connectors:

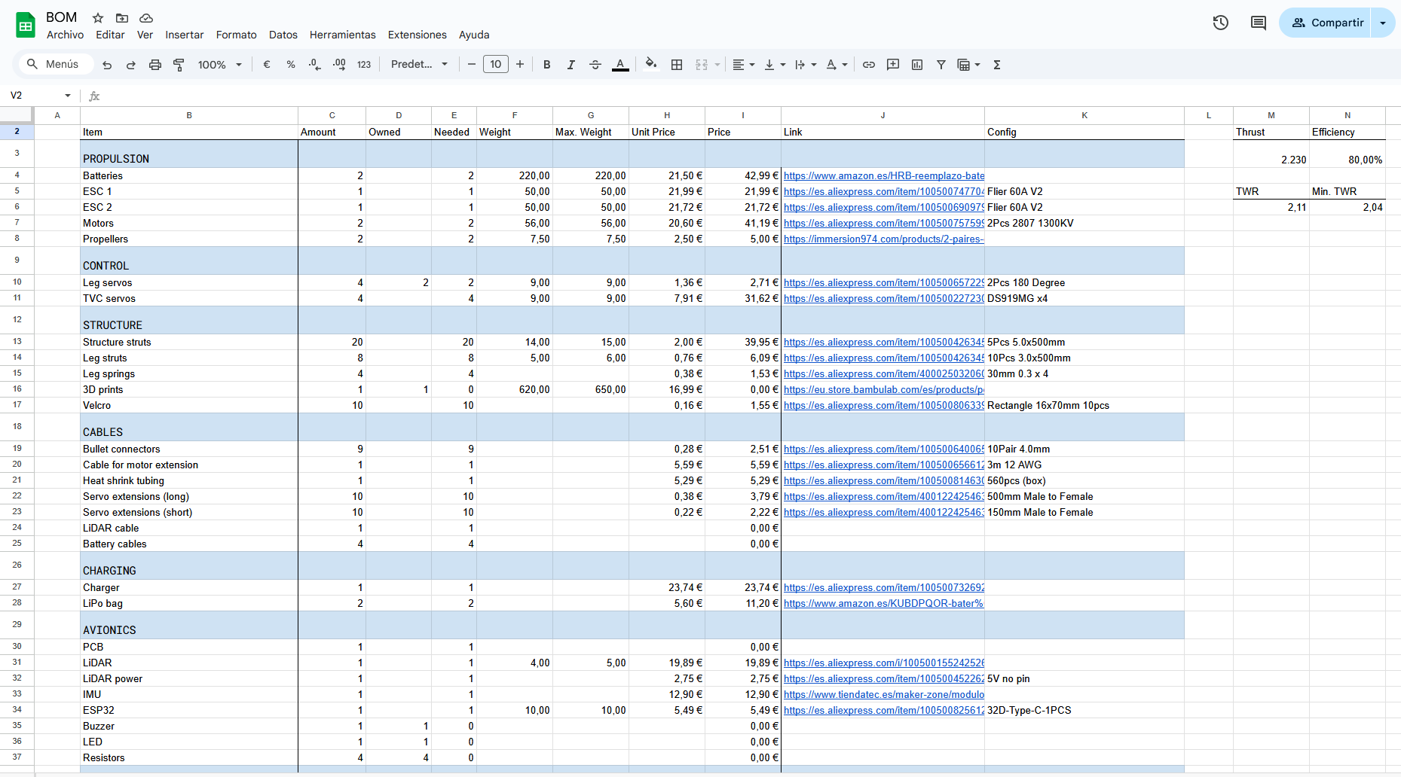
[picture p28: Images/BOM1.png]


Finally, I've created a new KiCAD project and I've begun making the schematic for the PCB and some custom symbols.

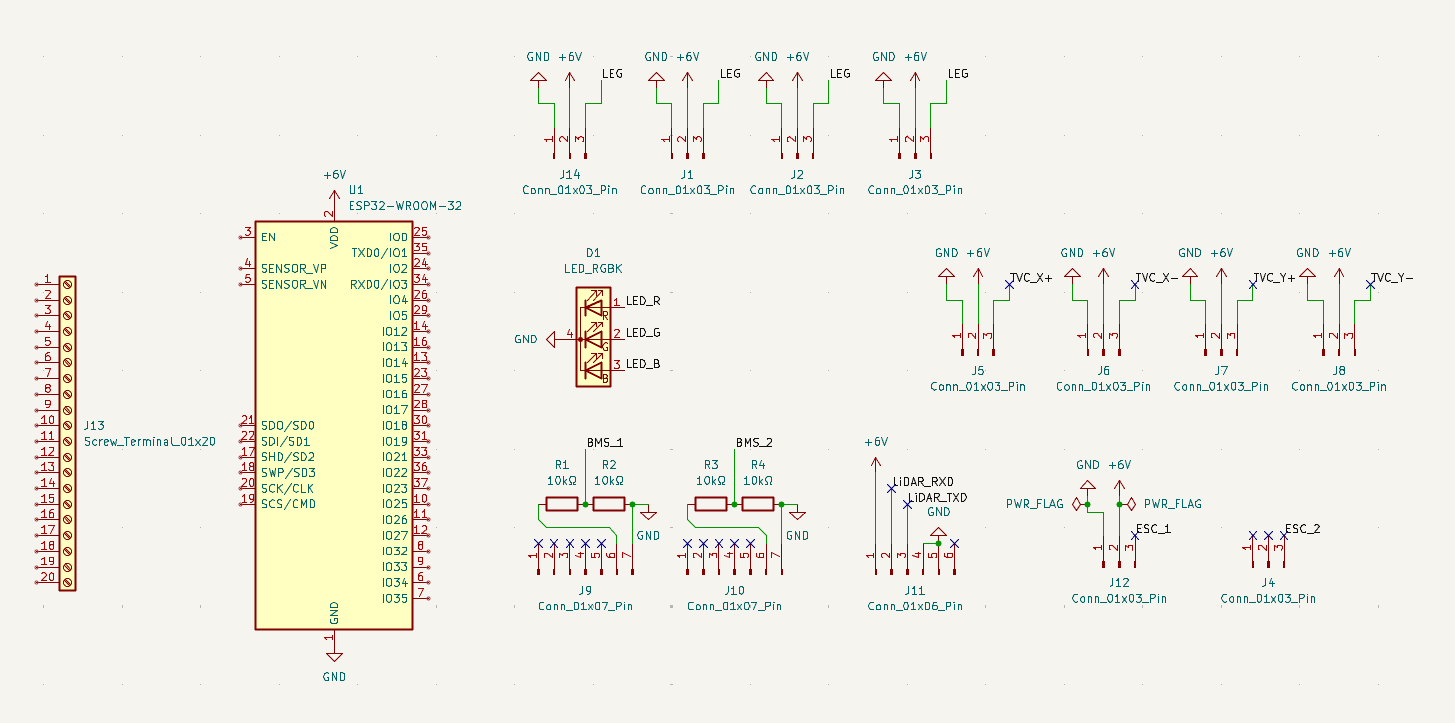
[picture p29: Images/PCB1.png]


**Time spent: 7h 30min**

## June 8: Finishing the schematic

Today I’ve created custom symbols for the ESP32, the buzzer and the MPU9250. With this I’ve made all the connections and finished making the schematic. I've also realized that I can configure one ESC to use 5V instead of 6, eliminating the need to use a voltage regulator for the LiDAR. Next, I’ll create custom footprints and start making the PCB layout.

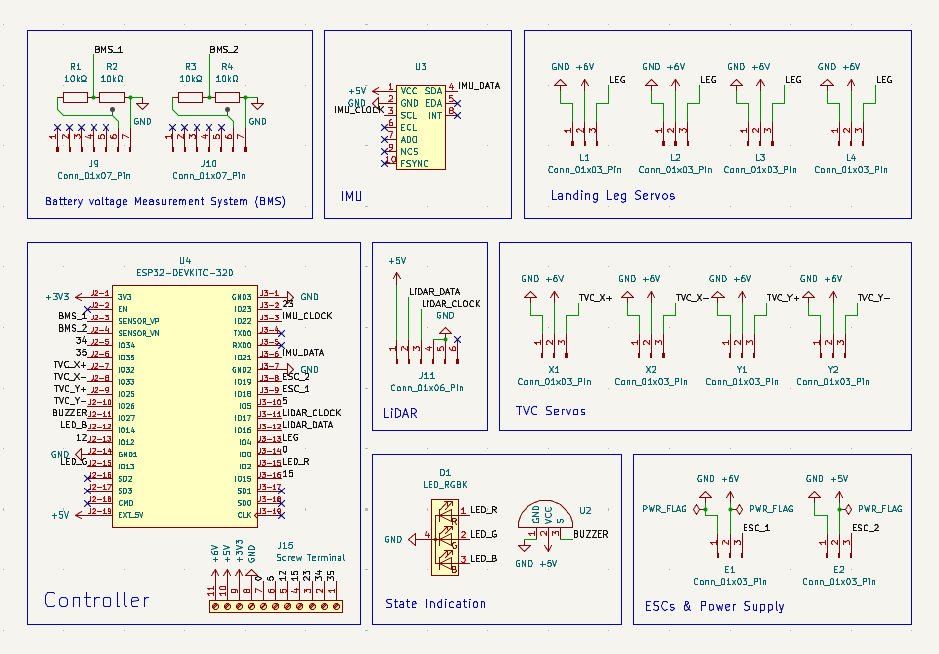
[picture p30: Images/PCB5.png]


**Time spent: 5h 30min**

## June 12: Starting the PCB layout

Today I've created or downloaded most footprints and 3D models and I've placed them on the PCB layout. This is my first PCB and I really like how it's looking so far. Next, I'll place the missing components and models and route the remaining traces.

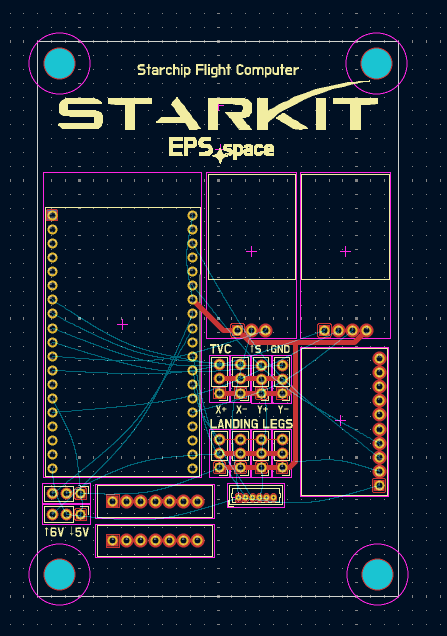
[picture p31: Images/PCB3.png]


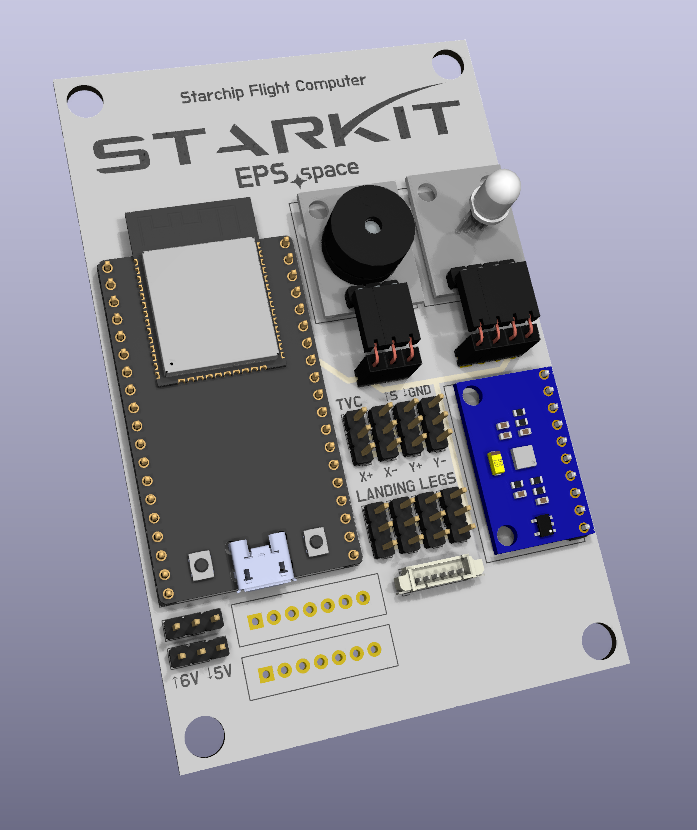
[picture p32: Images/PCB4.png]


**Time spent: 6h**

## June 13: Finishing the PCB

Today I've finished making and downloading the remaining footprints and 3D models, arranging the components on the PCB, routing the remaining traces and making the silkscreen. With this the PCB is complete!

Next, I'll finish the BOM and revise all components. After that I will send my project to online forums to make sure I haven't done any mistakes and that I have the most chances of succeeding.

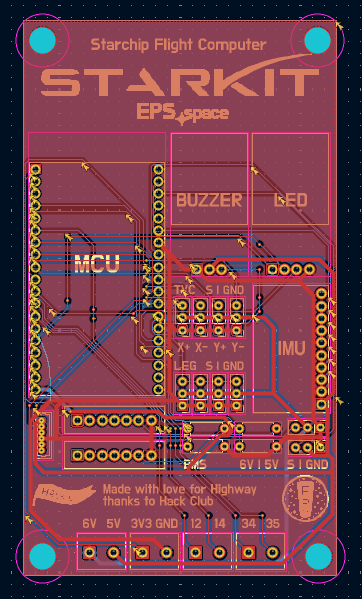
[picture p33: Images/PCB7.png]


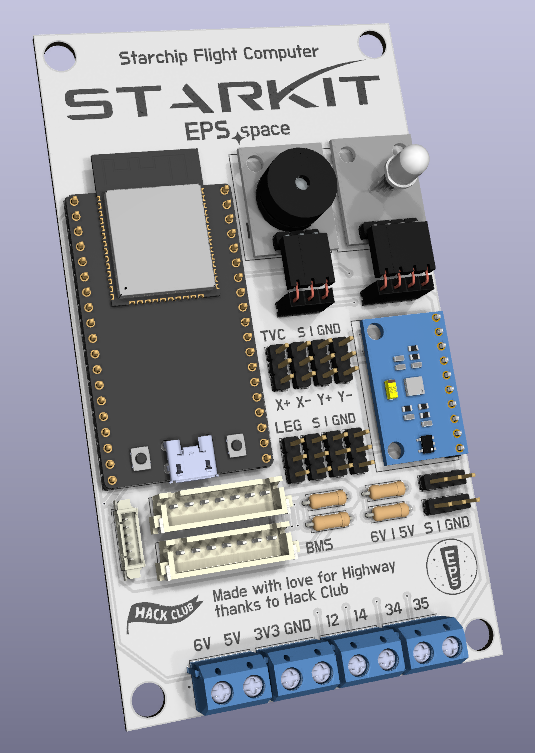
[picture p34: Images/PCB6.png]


**Time spent: 5h**

## June 14: Making a Unity simulation

My Internet decided not to work today so I started making a Unity simulation to better understand how the flight software would work. In the simulation, the rocket is capable of holding a predefined altitude and correcting its orientation with only the data that the real flight computer would have.

The following days I will work on the BOM and I’ll continue with the simulation after getting the project approved.

(Screenshot coming whenever I restore my Internet)

**Time spent: 3h**

## June 15 to 19: Updating the BOM

Over the past few days I've revised every component of the BOM and added some that were missing. I've gone through every component, searched for cheaper and better alternatives, and I've updated their weight and price. I've ended up switching a few connectors, so I will have to update that in the PCB as well. My Internet is still dead on my main PC so I will update the components and reroute the traces as soon as I can.

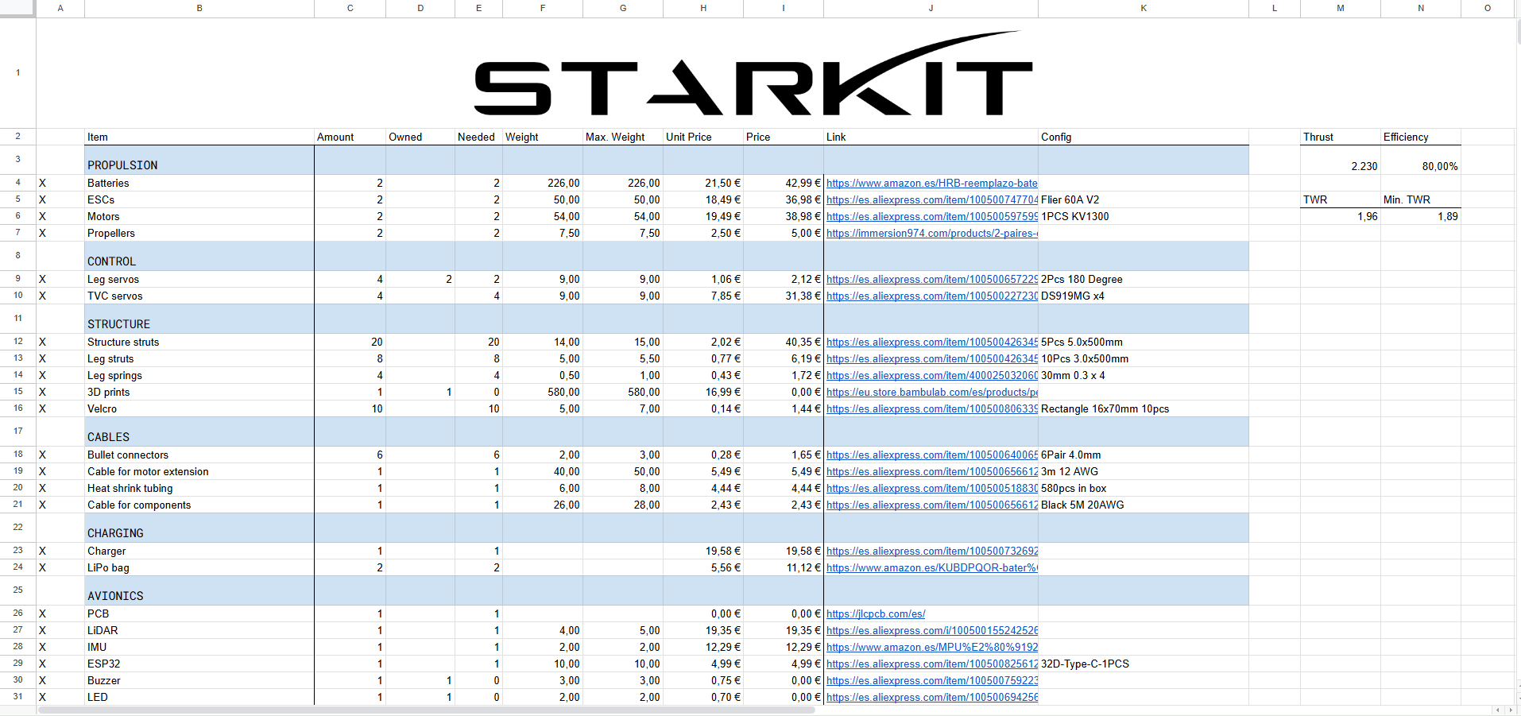
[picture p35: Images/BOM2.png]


**Time spent: 10h 45min across all days**

## June 21: Updating the PCB

In a combination of luck, hours of troubleshooting and miraculous circumstances I've managed to restore Internet connection on my main PC at about 1kbps. I've sent the KiCad files to my email and managed to open them on another computer.

After that I've updated the connectors that I had changed and I've rerouted the traces. Not only does the new design look nicer but it also has enough space to fit a picture of a silly kitten (the name "Starkit" comes from my obsession with cats anyways). I have also exported the PCB 3D model and attached it to its mount in the CAD model.

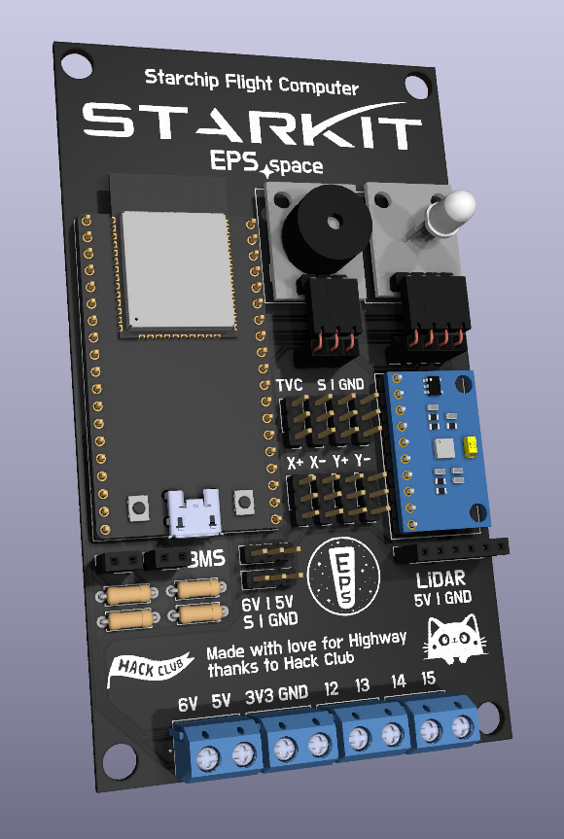
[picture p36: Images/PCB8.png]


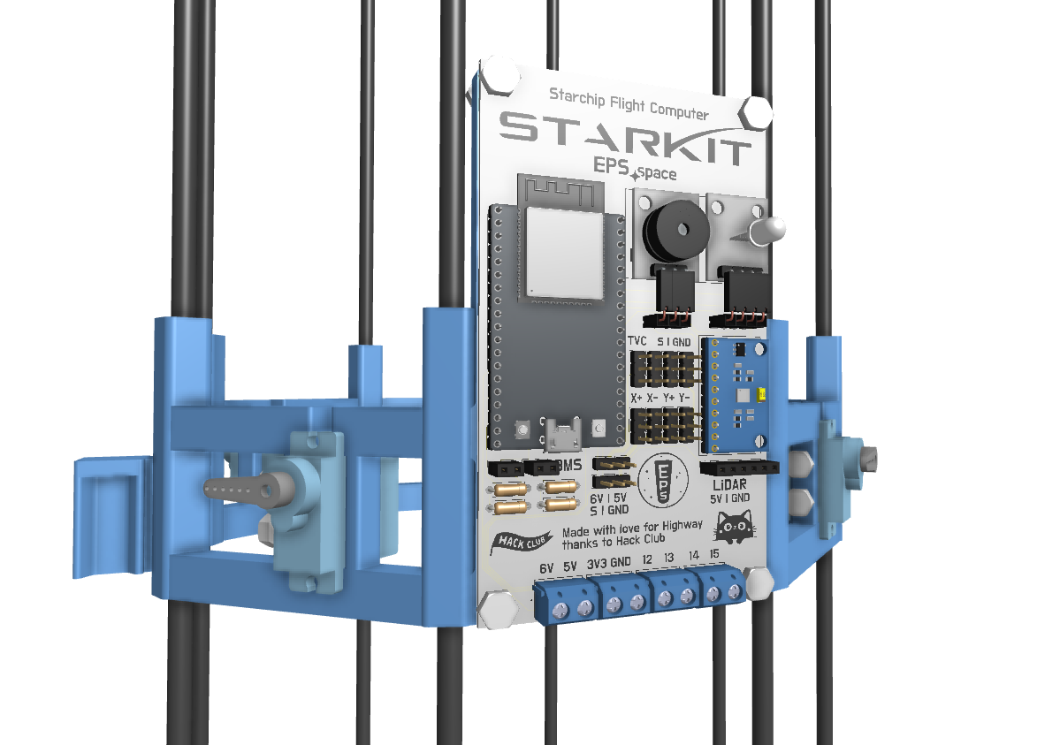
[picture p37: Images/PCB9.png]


**Time spent: 4h 30min**

## June 22: Tweaks to the CAD model and asking for design feedback

Today I've updated the CAD model slightly by adding bolts to lock carbon fiber rods to 3D prints, eliminating the need for glue. This should allow me to more easily replace rods or 3D printed parts when they break.

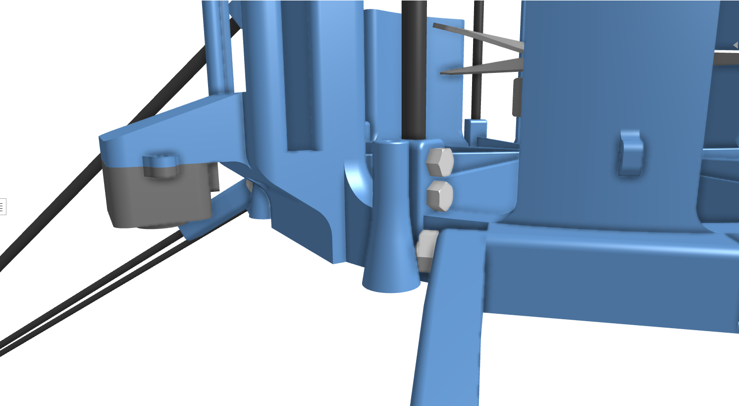
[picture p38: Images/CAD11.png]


After that I've written about the design of the rocket and asked for feedback on RC Groups, where there are people much more experienced than me that actually know what they're doing. With this I hope to make sure that I didn't make any major design flaw and that I have the most chances of succeeding.

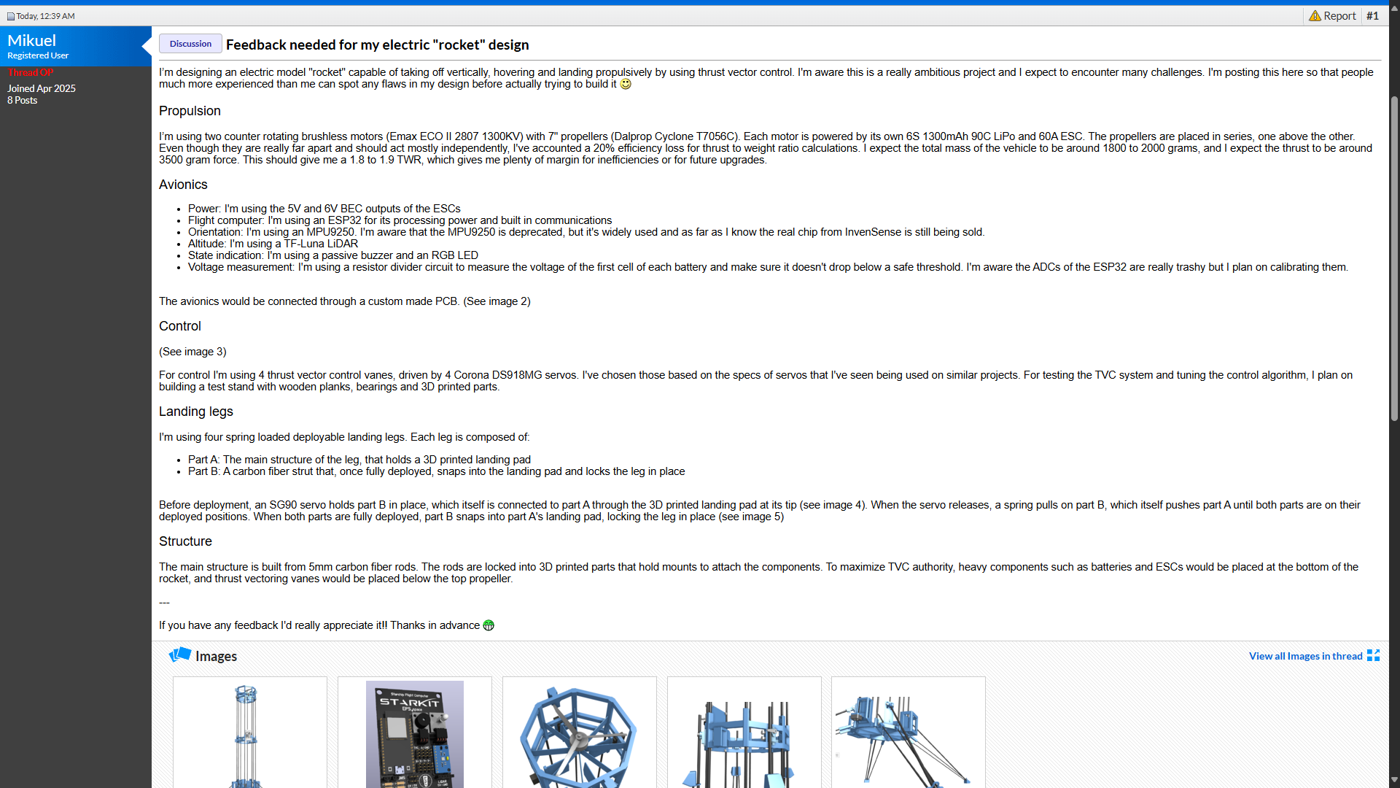
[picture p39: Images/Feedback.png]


**Time spent: 3h 30min**

## June 23: Preparations for submitting

People in RC Groups haven't spotted any major design flaws so far, so today I have started preparing my project for submission!

First, I have converted the BOM to CSV format and uploaded it to the project repo. Next, I have moved all of the PCB dependencies to a single folder and uploaded the KiCAD project to GitHub as well. Finally, I have updated the README following all of the submission requirements, including making a wiring diagram:



Finally, I have posted the project in #highway-pitstop and I'll see how it goes!

**Time spent: 3h**

---

# After getting approved

## July 3: Buying the parts!

I've got approved and I've just received the grant! Today I've checked which parts I could buy and receive in time before my trip and I've ended up buying the batteries and the LiPo bags.

**Time spent: 1h**

## July 4 to 6: The first parts have arrived

Over the past few days I've received the batteries and LiPo bags and I've uploaded their receipts to HCB!

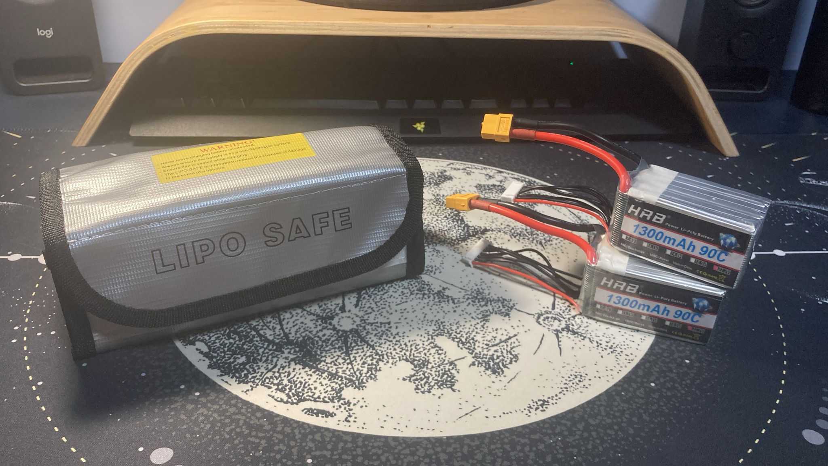
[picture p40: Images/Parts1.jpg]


## July 8: Prototyping servo mounts

Today I printed the landing leg servo mounts to see how they would behave.

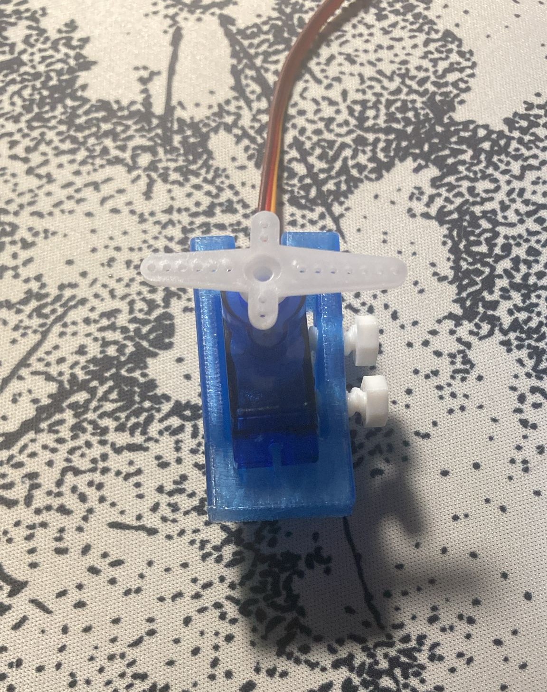
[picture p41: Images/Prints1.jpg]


Turns out, not really great. I was hoping for the friction from the bolts to prevent the servo from slipping, but this is not the case. In this prototype, the print can bend slightly, which wouldn't happen in the real thing, potentially increasing the friction. However, I've decided to redesign the servo mounts to make sure the servo will stay securely in place.



In the new design, the servo is pasted into a mount which can be bolted into the rocket's structure. This allows for easy replacement in case something breaks.



I printed a small section of the structure, which includes attachments for the rods which I plan on testing once I buy them. The bolts couldn't get in and I realized the rod attachments could flex, so I've made the necessary adjustments in the CAD model.

**Time spent: 6h**

## July 15: Adding items to my cart

Today I've added the items on AliExpress to my cart so that I can buy them when the shipping date is when I'm home.

**Time spent: 45min**

## July 21: Buying more parts

Today I've bought the carbon fiber rods, the IMU, the motors and the TVC servos.

Before buying them, I realized that the IMU had no reviews. Amazon, where I was planning to buy it, is plagued with fake MPU-9250s without magnetometers. For that reason I searched for other sellers and I found one on AliExpress with good reviews and a similar price that explicitly stated it used the original sensor with the magnetometer. I talked with my reviewer about the change, and after getting approved I bought all the parts!

**Time spent: 1h 15min**

## July 23: Attempting to buy more parts

Today I planned on buying the remaining items on AliExpress. I had already added them to my cart, and there happened to be a huge sale running that allowed me to get the LiPo charger for half the price. Now I just had to pay, or so I thought.

When I tried to pay, AliExpress declined my card for "security reasons". However it still had placed the order but I had to pay it within a certain timespan if I didn't want to get it cancelled. So I went through every one of the items and paid for them, except for the ESCs, the charger, the LiDAR and the leg springs, which I still couldn't pay. I kept trying and I eventually could pay the springs. Except because AliExpress chose to cancel my order right afterwards and now a refund will take 3 to 15 business days.

At this point it was 12PM and I decided to continue trying the day after. This meant that the order for the LiDAR would be cancelled, but that's fine as I didn't get any discounts on it. If I don't manage to pay for the charger tomorrow though I will lose $12 as I used my discount for that.

**Time spent: 1h 30min**

## July 24: Paying for the remaining parts

Today I attempted to pay for the remaining parts but it kept failing. As a last resort I called my father and we ended up opening a new PayPal account linked to the HCB card. This finally worked, and after paying for the ESCs and charger I ordered the remaining parts which I couldn't buy yesterday: the springs, the LiDAR and cables, which I couldn't add to my cart in the first place because of my order being too large.

I also noticed I had received the reimbursement from AliExpress, the one that allegedly would take 3 to 15 business days. Anyways the only things left to buy now are the propellers and the magnetic balancer. Except because I found out the store from which I was going to buy the propellers from doesn't ship anywhere at all, but that's a future me problem.

**Time spent: 1h**

## July 25: Finding new propellers

Today I wanted to buy the propellers, so I started looking for other sellers that would ship to my location. However, there weren't many as the propeller I chose is discontinued, and the only ones that I could find were way more expensive. I chose this propeller because of the availability of test data with the motors I'm using, but I started to look for other options. After some time I found out that the manufacturer of the propellers had made an updated version. Although I don't have test data for it, it should behave roughly the same. I found the propeller on Banggood at a good price, and I bought it after talking with my reviewer about the change.

**Time spent: 1h 15min**

## July 26: Buying the propeller balancer

Today I bought the propeller balancer and for once everything went according to plan. The only thing left to buy now is the PCB, which I'll do once I test the avionics.

## July 28: More parts have arrived!

Today the carbon fiber rods and the IMU have arrived!



## July 29 Log 1: The whole AliExpress warehouse has arrived at my room



I'm not even going to try to list everything that has arrived today. It's just insane to think that I got all of this for free.



After checking that everything was in a good state (and realizing that the AC cable for the charger had the wrong plug - thankfully I had spares), I organized everything into bags with different categories and all of that went into a box for everything Starkit.

**Time spent: 2h + 2h 30min organizing the rest of my electronics**

## July 29 Log 2: Testing the ESP32

The only thing left to buy is the PCB, but before I do that I have to verify that everything works fine as it is connected in the schematic. However, I decided to test every system in the avionics separately before assembling the whole circuit.

I had only worked with Arduinos before, not ESP32s, so I started by testing uploading an sketch to the ESP32 first. I followed through a 20 minute video on how to setup PlatformIO for ESP32 development. I installed the necessary drivers and adjusted the PlatformIO project settings but nothing worked at all. I tested different cables and different sketches but still I couldn't get it to work. Then I followed through a 1 minute video on how to setup Arduino IDE for ESP32. It worked on the first try an I got an LED to blink:



**Time spent: 1h 15min**

## July 30: Testing the LiDAR and the TVC servos

I started by testing the LiDAR with the ESP32. In the real thing, the LiDAR is powered by the BEC output of one of the ESCs. As the ESP32 is a 3V3 device, I had to use an Arduino UNO to provide the power. I made the following circuit:



After finding the right library and tweaking it to work with an ESP32, I got it to work pretty well.

Next, I tested the TVC servos. I used the same system in which I get the power from an Arduino but all processing happens on the ESP32. I got it working in no time and I was honestly surprised with their speed. A huge upgrade over the SG90s I had always worked with.



Finally, I soldered the IMU so that I can test it tomorrow.

**Time spent: 3hmin**

## July 31: Testing the IMU and the BMS

Today I wanted to test the two final subsystems of the avionics, the Inertial Measurement Unit and the Battery voltage Measurement System (get it???).

I wired the IMU up but when writing the code I realized I didn't even know what an I2C address was so I decided to do some research on how that works. And I learned that you can connect multiple devices to the same bus with only two wires. I just for some reason assumed each device needed two wires each. I decided to wire the LiDAR as well to the same bus, and after installing the necessary libraries and making the code, I got both the LiDAR and the IMU to work at the same time.



After that I installed a sensor fusion library and to my surprise it worked on the first try. It needed a bit of calibration on the raw IMU values for it not to drift over time, but the fact that I got sensor fusion to work so quickly is insane to me.

Next I updated the PCB to use a single I2C bus, as it simplifies the code, frees up pins and for my application it works the same. 

After that I tested the final subsystem, the BMS. It uses two 10kΩ resistors to divide the voltage of the first cell of each battery, so that the ESP32 can read it. After calibrating it I got it to work well at 5V and 3V3.



Finally I started working on making the full circuit, for which I planned to use the actual BEC outputs of the ESCs. However I forgot that without the motors connected (which I have to solder the connectors for) the ESCs can't make sounds and I can't calibrate them or configure them at different voltages. In the end I chose to not test the full circuit, as I've verified that every subsystem works and I prefer to solder the motor cables and connectors later on when the vehicle is assembled, so that I can choose the most optimal cable length.

**Time spent: 3h 30min**

## August 2 Log 1: More testing + Updating and ordering the PCB

Today I tested the LiDAR and the IMU again because I wanted to make sure that getting the data and performing sensor fusion wouldn't take over 20ms, which is the loop time the flight computer will be running at. At 400kHz of I2C clock speed it took only 2.5ms. The LiDAR allegedly only worked up to 250kHz but if it works it works.

Next, I made sure the dimensions and hole sizes for all the parts were correct on the PCB. I noticed that I had soldered the IMU headers with a slight slant so I wanted to solder the female headers on the PCB at an angle to compensate it. For that I needed to have the same hole size than in the IMU to align the headers, so I measured it on some pictures I found of the IMU and it appears to be 1.2mm.

Finally, I added the PCB to my cart on JLCPCB. I planned to buy it out of my own money, but as I updated some components and caught a discount on AliExpress I had enough money on the grant card to buy it. I talked to my reviewer about it and I got approved so I will buy it soon.

**Time spent: 3h**

## August 2 Log 2: More testing again

I realized on the rocket the LiDAR would be 50cm apart from the PCB, whereas the IMU would be mounted on it. This could cause issues when both are in the same bus, specially when running the LiDAR over its rated clock speed. I should have probably just used two buses and change the code of the libraries to work like that. Still I assembled the circuit again to test it with longer wires, and it still worked flawlessly.

**Time spent: 30min**

## August 5: Ordering the PCB

Today I ordered the PCB! Before that I changed the silkscreen slightly and I think it looks much better now.



**Time spent: 30min**

## August 20: The PCB has arrived!

The PCB has arrived today! It looks so sick



## August 22: Leg development

I've decided for my next project to be prototyping the landing legs. When making the CAD model I initially thought I could figure out how to cut the leg struts to be 45cm long, which allowed them to fit better with the deployable landing leg design. However, I decided to ditch that idea as I don't have a proper setup to cut them on. Carbon fiber can be pretty hazardous if gets into your lungs, eyes or skin, so I don't feel it would be wise to try cutting it without the necessary equipment.



Today I changed the design to work with 50cm struts. This makes the design heavier, but I still have plenty of weight budget to work with. Next, I started printing the parts to assemble a test leg. I sent the print job, and after a bed adhesion failure and some tweaking to the slicer settings, I got the first part of the assembly printed. I had tested the tolerances for the rods, but on my new part there was no way to get the rods in. Apparently printing orientation also plays an important role on the fit. I tried making the hole larger with no success, so I'll reprint the part tomorrow.



**Time spent: 2h**

## August 23: Leg development

Today I made a test piece to dial in the tolerance of the rods on that orientation. After knowing the optimal tolerance, I printed the part again. The rods got in, except because I quickly realized I had only changed one of the rods to be 50cm in the CAD model and I completely forgot that wasn't the only one I had planned on cutting.

I updated the design and printed it once again, except because only the fact that the hole was longer on the new design increased the friction enough to make fitting the rods impossible. At this point I had spent 90g of filament already so I really needed for my next attempt to go right. I dried the filament and printed more test pieces, and I think I dialed in the tolerance for this length, but I'll have to dry the filament more to get rid of all the bubbles which I think are currently preventing the rod from getting all the way through.

## August 24: Leg development

I think one of the reasons I had so much trouble yesterday is because I was constantly multitasking. When I had an issue, instead of reflecting on it I just tried random fixes and hit print, then went to work on other projects. While I might do other stuff when a part is being printed, I should have really reflected on my failures and worked on focused sessions to update the design.

Today, after drying the filament overnight, I printed more test pieces and after really making sure everything was right, I printed the full part. Except, guess what, it didn't fit yet again. For whatever reason, the same printing orientation, the same dimensions and the same slicer settings don't recreate the same hole on test pieces and on the real part. At this point I was kind of going insane so I just hit print again with more tolerance, but I paused the print at a few millimeters to test the fit before printing the full thing. Finally, after 120+ grams of filament and 2 rods that were sacrificed on test fits, I got the part to work. Going forward, having learnt how unpredictable this can be I will just make holes slightly oversized and use another locking mechanism such as hot glue, which would lock the rods firmly in place but also allows for remelting it if needed. It feels bad to have wasted so much material but at the same time the lessons I learnt cost much more than that.

After finally getting that part right, I printed the rest of parts of the assembly and the process was much more straightforward. The only thing left now is assembling everything.



**Time spent 2h 30min**

## August 25: Assembling the landing leg + Leg deployment mechanism

Today I assembled the landing leg prototype! Everything works as expected. Next, I printed the assembly that holds the servo to control the leg deployment. I had printed this previously to test the servo mounts but I'm printing it again with the changes I implemented. With this, I made a simple circuit to control the servo and I did my first ever leg deployment test.



**Time spent: 3h**

## August 29: Fixing the leg deployment mechanism

Today I wanted to fix a problem with the leg prototype that made the leg randomly deploy at times. The servo arm that held the leg in place before deployment wasn't long enough to account for the flex of the rod, so some movements and vibrations might flex the rod enough for the leg to deploy. To fix this, I printed a part that snaps into the servo arm to extend it. After a couple iterations I got it right!



After that, I cut some connectors to length to solder them to the PCB tomorrow.

**Time spent: 4h**

## August 30: Soldering the PCB

Today I started soldering the PCB!

**Time spent: 3h 15min**

## October 2nd: Soldering the remaining components

Today I soldered the remaining components to the PCB and I'm really happy with the result!



**Time spent: 2h 30min**

## October 3rd: Testing the PCB

Today I've tested all systems on the PCB except the BMS and the servos, which I will test soon. Again, I'm using an Arduino to provide the input voltage. This will be done by the ESCs on the real thing. Amazingly, everything worked flawlessly on the first try.



**Time spent: 1h 15min**

## October 5th: Testing the BMS and servos

Today I've tested the remaining systems on the PCB, the BMS and the servos. With this everything on the PCB is tested an I can move on to printing some more prototypes.


**Time spent: 1h**

## October 11th: Prototyping the battery and ESC mounts

The next thing I'm going to do is testing the battery, ESC, LiDAR and motor mounts. Today, I designed a test piece for the battery and ESC mounts. This piece also tests if the cables to connect the two are long enough, as arranged in the real thing. 

The test piece also includes two rod attachments with a new locking method that I'm testing using bolts. If this method were to be strong and reliable enough, I would use it to avoid the unpredictability of friction fits and to avoid using glue (which requires sanding the rods for strong adhesion, and I don't have the necessary equipment to do that).



The bad news: the cables aren't long enough and I don't have enough margin to move the mounts. The fix is really easy nonetheless, I'll just have to buy an male to female adapter which will extend the cables just enough.

The good news: bolt locking the rods works like a charm! No more testing tolerances or buying expensive equipment to sand the rods. I will now update the design to use this method everywhere.

**Time spent: 2h 45min**

## October 12: CADding

Today I adjusted the CAD model with the things I learnt from yesterday's prototype. With the prototype I also realized that the propellers that I've got are slightly larger from the ones I originally planned on using, which made the margin between the propeller and the print really low. I tried to make the diameter of the rocket larger, but my CAD model broke apart.

At this point there are many changes that I want to make, such as redesigning the airflow straighteners, using foam on the landing legs to reduce vibrations, changing all rod attachments to use 0.5mm of tolerance + a bolt lock, and changing the design to use only 1 rod segment instead of 2 (this will make the rocket shorter which is generally beneficial, and the new rod locking method allows me to attach prints in the middle of rod segments instead of in between them).

It became increasingly more obvious that with the mess that my CAD structure is I wouldn't be able to do all of this, so I decided to start over. I haven't made a lot of progress so far but I have a much cleaner structure from the beginning.

I've decided to split the model on 3 modules: the propulsion module at the bottom, the guidance module at the middle and the control module at the top.



**Time spent: 2h 45min**
  
## October 15th: Progress on the propulsion module

Today I continued working on the new CAD model. First, I added attachments for the carbon fiber rods on the propulsion module:



I then added the redesigned airflow straighteners, which will hold the motor and on the new model, the LiDAR as well.



Next, I added mounts for the ESCs:



Finally, I added the battery mounts:



**Time spent: 1h**

## October 16th: Progress on the new CAD model

Today I started working on the guidance module. I've made a structure with attachments for the rods and for the PCB.


  
Next, I added attachments for the landing leg servos:



I then started the design of the control module. I've added rod attachments and mounts for the TVC servos as well.



After that, I've set up an assembly that joins all modules and the carbon fiber rods.



Next I've added attachments for the landing legs on the propulsion module:



After that, I've added an attachment for the LiDAR below the motor. This new position will make it easier to solve altitude in code, and it makes the attachment lighter as well.



Finally, I added the motor mount on the propulsion assembly and I added fillets on everything. The propulsion assembly is almost finished!



**Time spent: 2h 30min**

## October 17th: Progress on the new CAD model

Today I started by adding the motor mount on the control assembly.



Next, I added the servos for leg deployment to the guidance assembly.



I then added the TVC servos and vanes to the control assembly.



Next, I made the landing legs:





After that, I added some foam to reduce vibrations on deployment.



I then added the PCB to the guidance module.



Finally, I added rod locking bolts in the propulsion and guidance assemblies.





**Time spent: 5h 15min**

## October 19th: Polishing the new CAD model

Today I added bolts for locking the carbon fiber rods to the control module as well



After that I added drafts on airflow straighteners to strengthen their joint with the structure.



**Time spent: 30min**

## October 21st: Polishing the new CAD model

Today I added some rod locking bolts that were missing on the landing legs.





With this the new CAD model is complete!





**Time spent: 30min**

## October 24th: Designing prototypes

Today, I made some prototypes to test some parts of the new design. This prototype tests the motor mount and the LiDAR mount:



And this prototype tests the attachment for the TVC vanes:



**Time spent: 15min**

## October 25th: Prototyping

Today I printed the test pieces I had designed yesterday. The bolts for holding the motor wouldn't fit, so I adjusted the CAD model to fix that.



I also printed the piece to test the attachment for the TVC vanes and everything worked as expected.

## October 26th: Rotating LiDAR mount

Today I rotated the LiDAR sensor on the bottom because I noticed its cable to the PCB would be shorter this way.



**Time spent: 15min**

## November 1st: Weight optimizations

Today I woke up and realized that I could make a simple change on the design and save a lot of mass. First, I removed the servos for leg deployment from the guidance assembly, leaving the PCB mount only.



Next, I moved the servos for leg deployment to the control assembly.



Finally, I updated the assemblies to use the new design.







With this change, the guidance assembly weighs basically nothing, and the control assembly doesn't weigh that much more because it had already got the structure to hold servos.

At this point I'm happy with the design and I've tested and prototyped everything that I wanted to. I'm finally going to start building this thing and see how it goes!

**Time spent: 1h 30min**

---

# Building Starkit

## October 26: Printing the first module

Today I printed the first module of Starkit, the propulsion module. After cancelling the first print early on because I had forgotten a support, I let the second print run overnight and I woke up to a beautiful first module! (I actually woke up multiple times over the night because the filament kept tangling)

With this Starkit officially goes from CAD to reality!

## October 27: Post processing and assembly

Today I removed all support material from the module and assembled a mock up to see how the rocket will look. I'm so excited this is finally becoming real!



**Time spent: 30min**

## November 6th: Printing bolts + Starting code

Today I've printed rod locking bolts for the propulsion module. I've also started coding the flight software while I wait for prints. For now the rocket is able to read its sensors and I'm able to easily switch between getting data from the sensors or from a simulation.

**Time spent: 2h**

## November 7th

Today I've continued coding the flight software for Starkit. I've implemented PID algorithms which Starkit is now able to use to correct its orientation through the TVC servos.

**Time spent: 4h 30min**

## November 8th: Developing flight software features

Today I've continued making the flight software.

- Starkit is now able to correct its altitude through the throttle of the motors
- Sensor fusion now works when the IMU is vertical, as it is in the rocket
- All TVC axis work now for correcting the rocket's orientation
- A state machine now manages the flight phases according to a predefined flight profile

**Time spent: 5h 30min**

## November 15th: Printing landing leg tops

Today I printed the top part of the landing legs, which acts as a hinge and attaches to a spring for the leg to deploy.

## November 16th: Attaching batteries

Today I attached the batteries to the propulsion module using velcro.

**Time spent: 15min**

## November 18th: Preparing guidance module print

Today I prepared the guidance module for printing.

**Time spent: 15min**

## November 20th: Printing and assembling landing leg

Today I printed the first landing leg and assembled it. I've noticed that with the 3mm rods, the bolt locks slip under stress, which is problematic since landing legs need to support the entire weight of the rocket. 5mm rods would probably slip much less due to increased contact area with the bolt. Thankfully, I made the rocket shorter and I have just the right amount of 5mm rods left over to do this, so I will test how it performs soon.

## December 4th (my birthday!): Testing 5mm rods in landing legs 

Today I wanted to try replacing the 3mm rods in the landing legs with 5mm ones. I made the necessary changes in the CAD model and printed the updated parts.

Unfortunately I've noticed even with 5mm rods and more bolts, bolt locking simply is not enough for the stress those parts are facing. Also, that PLA bolt that supports all the weight from the landing legs broke. I really need something stronger, because every time it breaks there's a chance it gets stuck on the module and I have to reprint the whole thing, which is 350g of filament. Plus I can't have it break when it's supporting the whole weight of the rocket.

**Time spent: 1h 15min**

## December 7th: Testing PETG and shock absorbers

Today I wanted to test replacing the PLA bolt with a PETG cylinder, printed horizontally for more strength. While the filament was drying, I tried to start cutting the foam I wanted to add to reduce vibrations on leg deployment, but it was so small it was very difficult to cut and it barely cushioned. Because of this, I designed a 3D printed flexible shock absorber.

The result? An almost perfect landing leg! The PETG cylinder is holding up well. The landing leg tip is slipping slightly but I've already redesigned that for about the 10th time and I just have to print the updated version. I have to iterate on the shock absorbers as well but overall, everything is working as I wanted for it to.

**Time spent: 1h 45min**

## December 13th: Printing updated landing leg parts

I've printed the updated leg tip, a stronger PETG cylinder, and the updated shock absorbers. The shock absorbers spaghettified, but with the rest of the parts I was able to assemble an almost perfect landing leg! I will print the updated shock absorbers tomorrow.

**Time spent: 1h**

## December 14th: Printing and assembling landing leg

Today I printed the updated shock absorbers, pasted them and finally assembled the perfect landing leg! The updated shock absorbers do a really good job, and I'm now comfortable to print the 3 remaining legs, so I started printing all the parts required for assembling another one.

**Time spent: 30min**

## January 7th: Printing the remaining landing legs

Today I printed the parts for the 2 remaining landing legs.

**Time spent: 15min**

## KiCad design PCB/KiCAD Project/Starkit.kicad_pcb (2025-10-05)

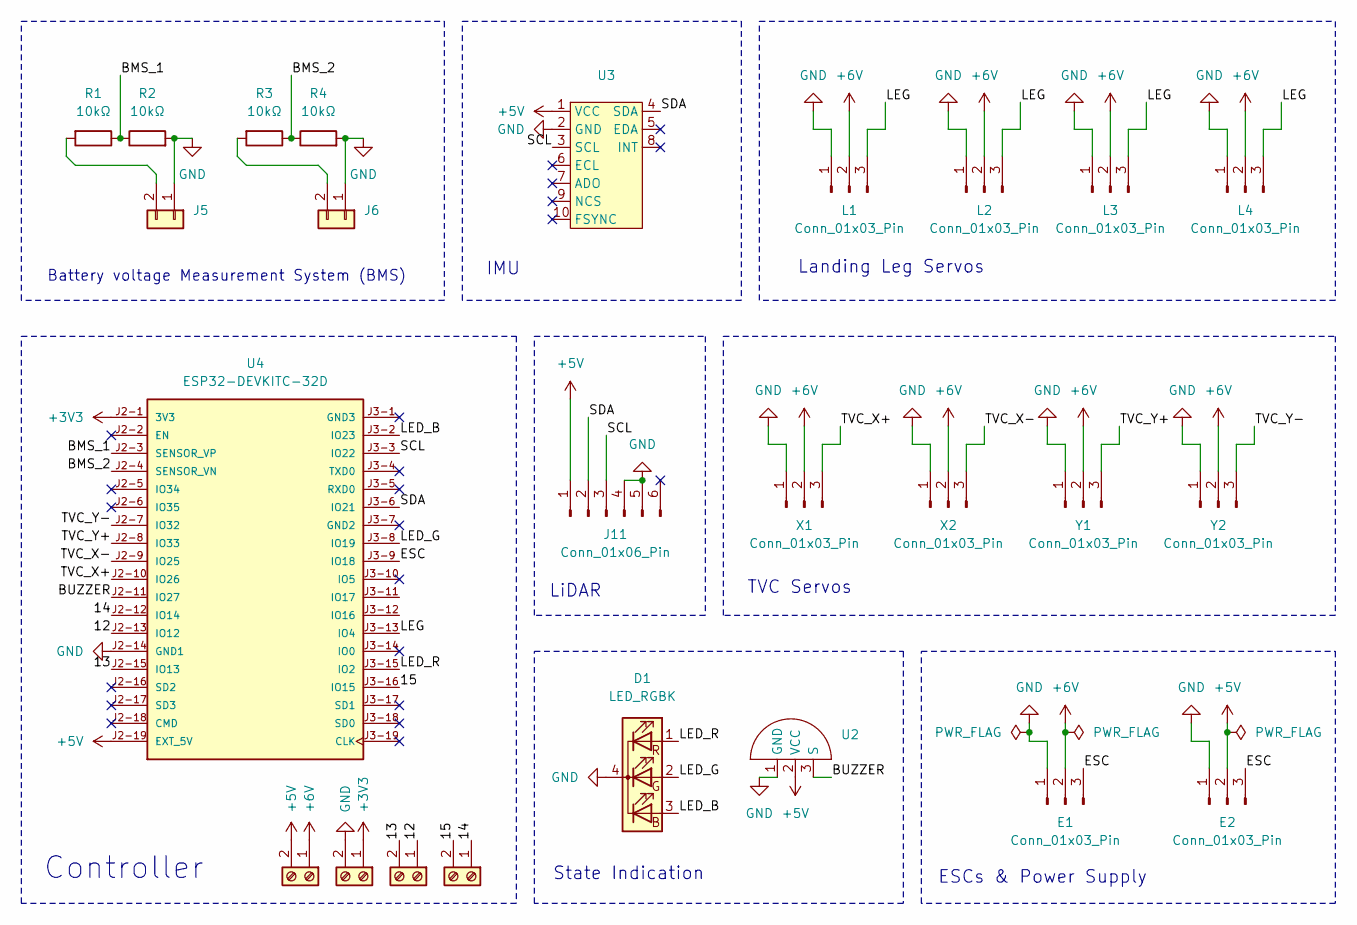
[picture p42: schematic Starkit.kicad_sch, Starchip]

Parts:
D1: LED_RGBK; KY-016
E1, E2: Conn_01x03_Pin; PinHeader_1x03_P2.54mm_Vertical
J1, J2, J3, J4: Screw_Terminal_01x02; HANDSON_KF301-2P
J5, J6: Conn_01x02; PinSocket_1x02_P2.54mm_Vertical
J11: Conn_01x06_Pin; PinSocket_1x06_P2.54mm_Vertical
L1, L2, L3, L4: Conn_01x03_Pin; PinHeader_1x03_P2.54mm_Vertical
R1, R2, R3, R4: 10kΩ; R_Axial_DIN0207_L6.3mm_D2.5mm_P7.62mm_Horizontal
U2: KY-012
U3: GY-9250
U4: ESP32-DEVKITC-32D; MODULE_ESP32-DEVKITC-32D; PARTREV V4; DigiKey_Part_Number 1965-1000-ND
X1, X2: Conn_01x03_Pin; PinHeader_1x03_P2.54mm_Vertical
Y1, Y2: Conn_01x03_Pin; PinHeader_1x03_P2.54mm_Vertical

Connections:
+3V3: J2.1, U4.J2-1 (3V3)
+5V: E2.2, J1.2, J11.1, U2.2 (VCC), U3.1 (VCC), U4.J2-19 (EXT_5V)
+6V: E1.2, J1.1, L1.2, L2.2, L3.2, L4.2, X1.2, X2.2, Y1.2, Y2.2
/12: J3.1, U4.J2-13 (IO12)
/13: J3.2, U4.J2-15 (IO13)
/14: J4.1, U4.J2-12 (IO14)
/15: J4.2, U4.J3-16 (IO15)
/BMS_1: R1.1, R2.1, U4.J2-3 (SENSOR_VP)
/BMS_2: R3.1, R4.1, U4.J2-4 (SENSOR_VN)
/BUZZER: U2.3 (S), U4.J2-11 (IO27)
/ESC: E1.3, E2.3, U4.J3-9 (IO18)
/LED_B: D1.3 (BA), U4.J3-2 (IO23)
/LED_G: D1.2 (GA), U4.J3-8 (IO19)
/LED_R: D1.1 (RA), U4.J3-15 (IO2)
/LEG: L1.3, L2.3, L3.3, L4.3, U4.J3-13 (IO4)
/SCL: J11.3, U3.3 (SCL), U4.J3-3 (IO22)
/SDA: J11.2, U3.4 (SDA), U4.J3-6 (IO21)
/TVC_X+: U4.J2-10 (IO26), X1.3
/TVC_X-: U4.J2-9 (IO25), X2.3
/TVC_Y+: U4.J2-8 (IO33), Y1.3
/TVC_Y-: U4.J2-7 (IO32), Y2.3
GND: D1.4 (K), E1.1, E2.1, J2.2, J5.1, J6.1, J11.4, J11.5, L1.1, L2.1, L3.1, L4.1, R2.2, R4.2, U2.1 (GND), U3.2 (GND), U4.J2-14 (GND1), X1.1, X2.1, Y1.1, Y2.1
unnamed: J5.2, R1.2
unnamed: J6.2, R3.2

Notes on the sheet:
IMU
Battery voltage Measurement System (BMS)
Landing Leg Servos
Controller
LiDAR
ESCs & Power Supply
TVC Servos
State Indication

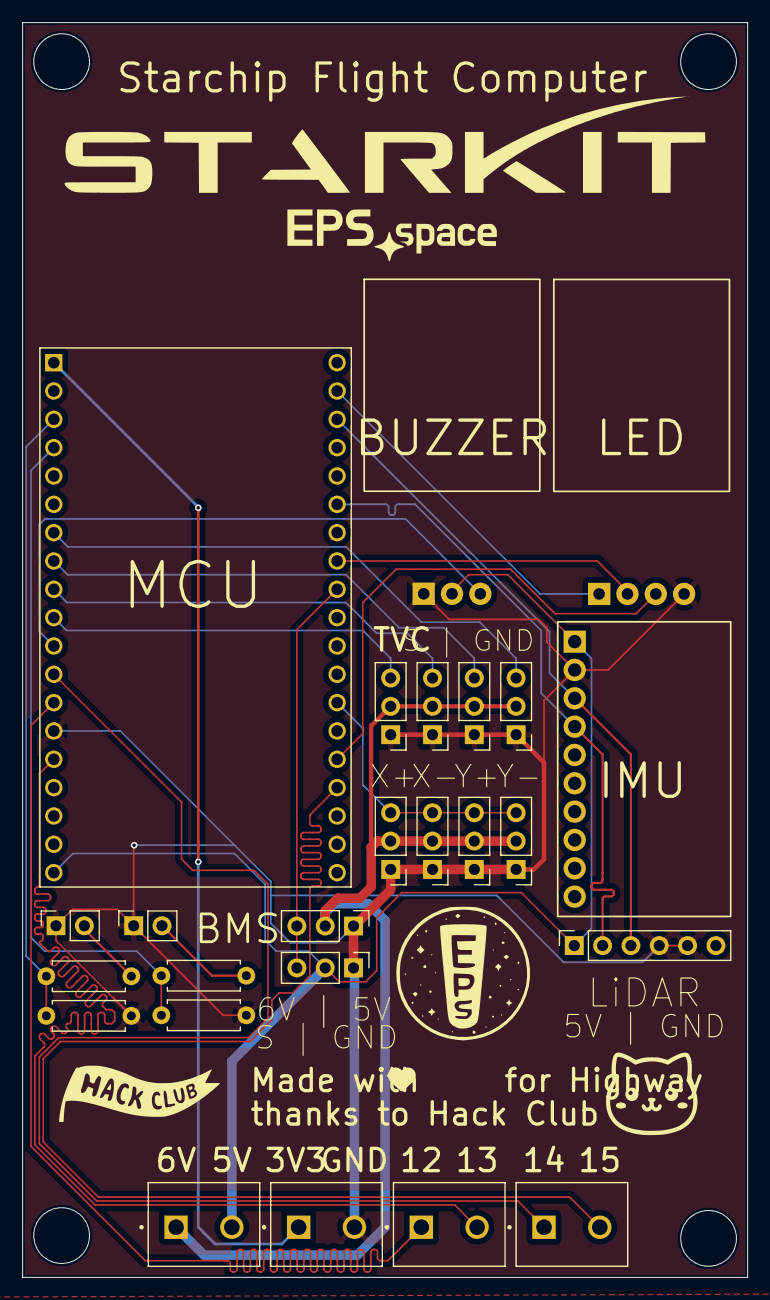
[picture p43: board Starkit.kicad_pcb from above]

Board: 2 copper layers, 65.0 x 112.5 mm, 25 parts (0 on the bottom side), 24 nets.
